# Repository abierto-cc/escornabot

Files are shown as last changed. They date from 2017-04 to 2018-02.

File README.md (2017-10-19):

# furubot

Diseño de robot basado en el Escornabot, completamente hecho en KiCAD. 

Con amor para todo el mundo desde Malmo - Suecia.

# créditos

Los creadores originales de Escornabot www.escornabot.com y su comunidad de usuarios y desarrolladores 

# autor

J. Garcia at abierto.cc

# abierto

Abierto es una inciativa de D. Cuartielles gracias a la generosa aportación de la Fundación PUIG por intermediación de la Fundación Ashoka de cara a contribuir a la creación de material educativo de libre acceso y circulación

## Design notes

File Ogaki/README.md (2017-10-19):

# Escornabot Ogaki

Diseño de robot basado en el Escornabot, completamente hecho en KiCAD. 

Con amor para todo el mundo desde Malmo - Suecia.

# consigue tu kit

Si quieres conseguir el kit para montarlo, visita: https://abierto.cc/shop

# instrucciones de montaje

Puedes ver las instrucciones de montaje paso a paso en: https://sites.google.com/abierto.cc/ogaki

# créditos

Los creadores originales de Escornabot y su comunidad de usuarios y desarrolladores

# autor

J. Garcia at abierto.cc

# abierto

Abierto es una inciativa de D. Cuartielles gracias a la generosa aportación de la Fundación PUIG por intermediación de la Fundación Ashoka de cara a contribuir a la creación de material educativo de libre acceso y circulación

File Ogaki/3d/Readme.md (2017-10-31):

Modelos 3D del Escornabot Ogaki a.k.a. Brivori Compactus v3
===========================================================

Estos son los modelos 3D listos para imprimir para el Escornabot Ogaki. Los ficheros son copias de seguridad de los originales creados por la comunidad Escornabot. Más concretamente:

* El diseño original es por [Xoan Sampaiño][XOA01] ([License MIT][LIC01])
* Las ruedas son de [Rafa
Couto](https://github.com/rafacouto/3d-models/tree/master/escornabot/stronger-wheel) 
* La pieza de sujección de la CPU "EscornaCPU" está basada en el diseño de placa de  [Xabier Rosas](https://github.com/escornabot/electronics).

# Ficheros STL listos para impresión

- Ball-caster [ballcaster.stl](ballcaster.stl)
- Battery bracket [battery-bracket.stl](battery-bracket.stl)
- Motor bracket [motor-bracket.stl](motor-bracket.stl)
- Left wheel [wheel-l.stl](wheel-l.stl)
- Right wheel [wheel-r.stl](wheel-r.stl)
- EscornaCPU 3.00 bracket [escornacpu-3\_00-bracket.stl](escornacpu-3_00-bracket.stl)

Los ficheros fuentes están también en esta carpeta

[LIC01]: brivoi-compactus/LICENSE
[XOA01]: https://github.com/xoan/escornabot

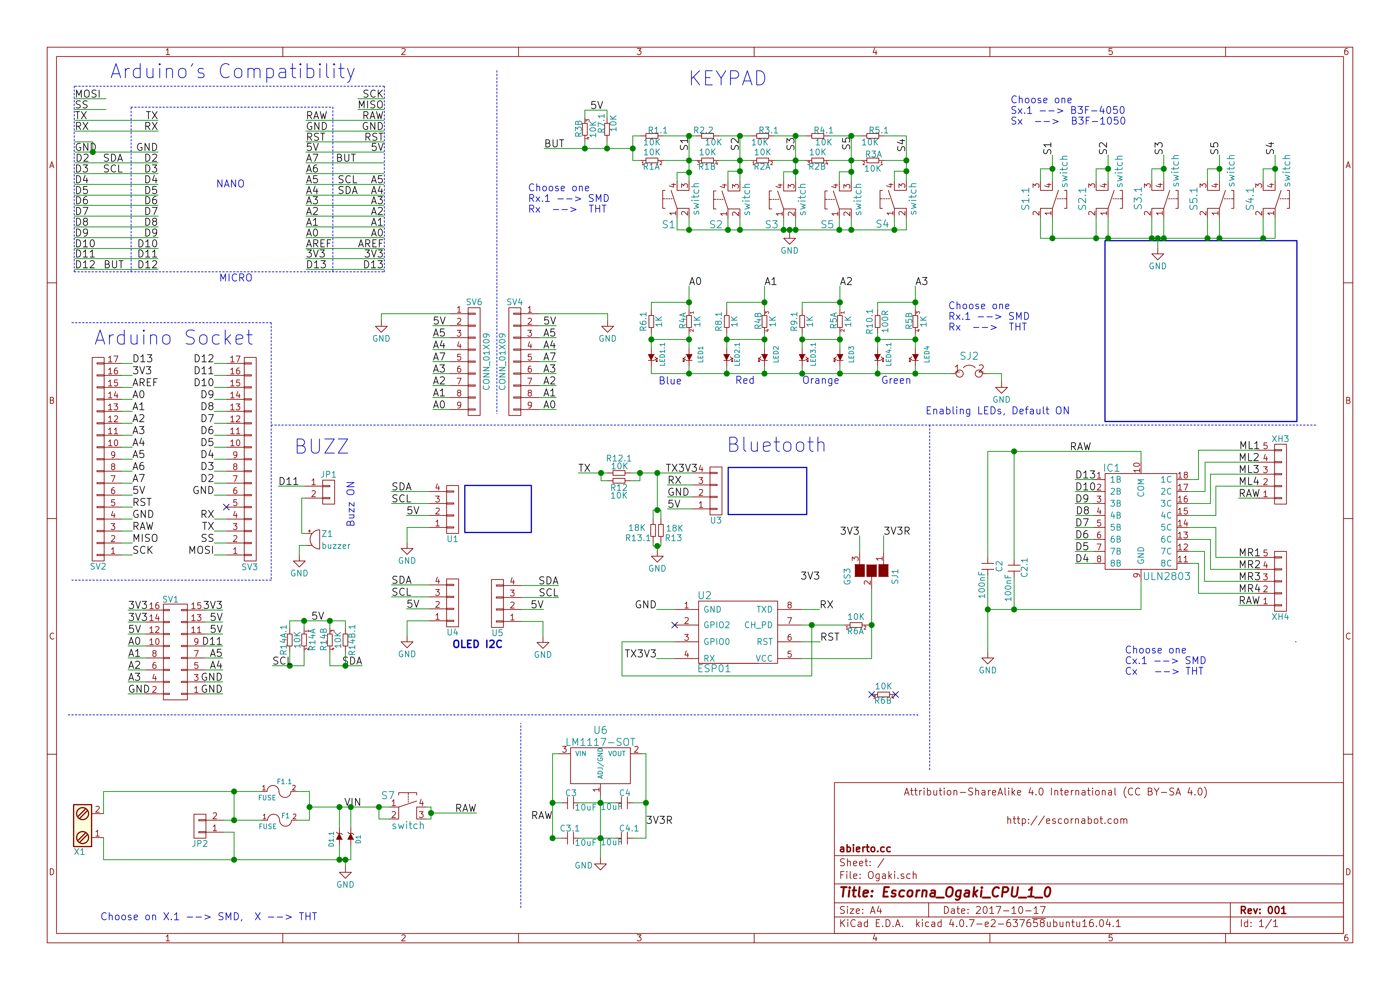
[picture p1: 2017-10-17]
Ogaki/hardware/pdf/Ogaki.png

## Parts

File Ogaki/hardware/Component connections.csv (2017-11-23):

Arduino micro | Arduino Nano | Component
D0 |  |  | D0 | Buetooth (Rx)
D1 |  |  | D1 | Buetooth (Tx)
D2 |  |  |  | Oled (SDA)
D3 |  |  |  | Oled (SCL)
D4 |  |  | D4 | Motor
D5 |  |  | D5 | Motor
D6 |  |  | D6 | Motor
D7 |  |  | D7 | Motor
D8 |  |  | D8 | Motor
D9 |  |  | D9 | Motor
D10 |  |  | D10 | Motor
D11 |  |  | D11 | Buzzer
D12 (A11) |  |  | Buttons
D13 |  |  | D13 | Motor
A0 |  |  | A0 | LED Blue
A1 |  |  | A1 | LED Red
A2 |  |  | A2 | LED Orange
A3 |  |  | A3 | LED Green
 |  |  | A4 | Oled (SDA)
 |  |  | A5 | Oled (SCL)
A6 |  |  | A6
 |  |  | A7 | Buttons

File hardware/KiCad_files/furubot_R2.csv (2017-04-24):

Reference | Value | Footprint | Datasheet
SV1 | CONN_02X08 | Pin_Headers:Pin_Header_Straight_2x08_Pitch2.54mm
R7.1 | 10K | Resistors_SMD:R_0603_HandSoldering
R1.1 | 10K | Resistors_SMD:R_0603_HandSoldering
R3.1 | 10K | Resistors_SMD:R_0603_HandSoldering
R4.1 | 10K | Resistors_SMD:R_0603_HandSoldering
R5.1 | 10K | Resistors_SMD:R_0603_HandSoldering
R2.2 | 10K | Resistors_SMD:R_0603_HandSoldering
S1 | switch | Switch:Button
S2 | switch | Switch:Button
S5 | switch | Switch:Button
S4 | switch | Switch:Button
S5.1 | switch | Buttons_Switches_ThroughHole:SW_PUSH_6mm
S4.1 | switch | Buttons_Switches_ThroughHole:SW_PUSH_6mm
S2.1 | switch | Buttons_Switches_ThroughHole:SW_PUSH_6mm
S3.1 | switch | Buttons_Switches_ThroughHole:SW_PUSH_6mm
S1.1 | switch | Buttons_Switches_ThroughHole:SW_PUSH_6mm
S3 | switch | Switch:Button
R6.1 | 1K | Resistors_SMD:R_0603_HandSoldering
R8.1 | 1K | Resistors_SMD:R_0603_HandSoldering
R9.1 | 1K | Resistors_SMD:R_0603_HandSoldering
R10.1 | 100R | Resistors_SMD:R_0603_HandSoldering
LED1.1 | L | LEDs:LED_0603
LED1 | L | LEDs:LED_D3.0mm
LED2.1 | L | LEDs:LED_0603
LED2 | L | LEDs:LED_D3.0mm
LED3.1 | L | LEDs:LED_0603
LED3 | L | LEDs:LED_D3.0mm
LED4.1 | L | LEDs:LED_0603
LED4 | L | LEDs:LED_D3.0mm
SJ2 | JUMPER | Connect:GS2
JP1 | CONN_01X02 | Pin_Headers:Pin_Header_Straight_1x02_Pitch2.54mm
Z1 | buzzer | Buzzers_Beepers:MagneticBuzzer_StarMicronics_HMB-06_HMB-12
U1 | CONN_01X04 | Pin_Headers:Pin_Header_Straight_1x04_Pitch2.54mm
U4 | CONN_01X04 | Pin_Headers:Pin_Header_Straight_1x04_Pitch2.54mm
U5 | CONN_01X04 | Pin_Headers:Pin_Header_Straight_1x04_Pitch2.54mm
U3 | CONN_01X04 | Pin_Headers:Pin_Header_Straight_1x04_Pitch2.54mm
R12.1 | 10K | Resistors_SMD:R_0603_HandSoldering
R12 | 10K | Resistors_ThroughHole:R_Axial_DIN0204_L3.6mm_D1.6mm_P7.62mm_Horizontal
R13.1 | 18K | Resistors_SMD:R_0603_HandSoldering
R13 | 18K | Resistors_ThroughHole:R_Axial_DIN0204_L3.6mm_D1.6mm_P7.62mm_Horizontal
IC1 | ULN2803 | Housings_DIP:DIP-18_W7.62mm_Socket
C2 | 100nF | Capacitors_ThroughHole:C_Disc_D5.0mm_W2.5mm_P5.00mm
C2.1 | 100nF | Capacitors_SMD:C_0603_HandSoldering
X1 | Screw_Terminal_1x02 | Connect:bornier2
JP2 | CONN_01X02 | Pin_Headers:Pin_Header_Angled_1x02_Pitch2.54mm
F1.1 | FUSE | Resistors_SMD:R_1206_HandSoldering
F1 | FUSE | Fuse_Holders_and_Fuses:Fuse_TE5_Littlefuse-395Series
D1.1 | ZENER | Diodes_SMD:D_0603
D1 | ZENER | Diodes_ThroughHole:D_DO-41_SOD81_P10.16mm_Horizontal
C1 | 100nF | Capacitors_ThroughHole:C_Disc_D5.0mm_W2.5mm_P5.00mm
C1.1 | 100nF | Capacitors_SMD:C_0603_HandSoldering
U2 | ESP01 | escornabot:ESP01
XH4 | CONN_01X05 | user_molex:B5B-XH-A
XH3 | CONN_01X05 | user_molex:B5B-XH-A
R3 | 10K | Resistors_ThroughHole:R_Array_SIP4
R1 | 10K | Resistors_ThroughHole:R_Array_SIP4
R2 | 10K | Resistors_ThroughHole:R_Array_SIP4
R4 | 1K | Resistors_ThroughHole:R_Array_SIP4
R5 | 1K | Resistors_ThroughHole:R_Array_SIP4
R6 | 10K | Resistors_ThroughHole:R_Array_SIP4
S7 | switch | ComponentesVarios:on_off_Switch
SV2 | CONN_01X17 | Pin_Headers:Pin_Header_Straight_1x17_Pitch2.54mm
SV3 | CONN_01X17 | Pin_Headers:Pin_Header_Straight_1x17_Pitch2.54mm
U6 | LM1117-SOT | TO_SOT_Packages_THT:TO-220_Vertical
C4 | 10uF | Capacitors_ThroughHole:C_Disc_D5.0mm_W2.5mm_P5.00mm
C3 | 10uF | Capacitors_ThroughHole:C_Disc_D5.0mm_W2.5mm_P5.00mm
C3.1 | 10uF | Capacitors_SMD:C_0603_HandSoldering
C4.1 | 10uF | Capacitors_SMD:C_0603_HandSoldering
SJ1 | GS3 | Connect:GS3
SV4 | CONN_01X09 | Pin_Headers:Pin_Header_Straight_1x09_Pitch2.54mm
SV6 | CONN_01X09 | Pin_Headers:Pin_Header_Straight_1x09_Pitch2.54mm
R14 | 10K | Resistors_ThroughHole:R_Array_SIP4
R14A.1 | 10K | Resistors_SMD:R_0603_HandSoldering
R14B.1 | 10K | Resistors_SMD:R_0603_HandSoldering

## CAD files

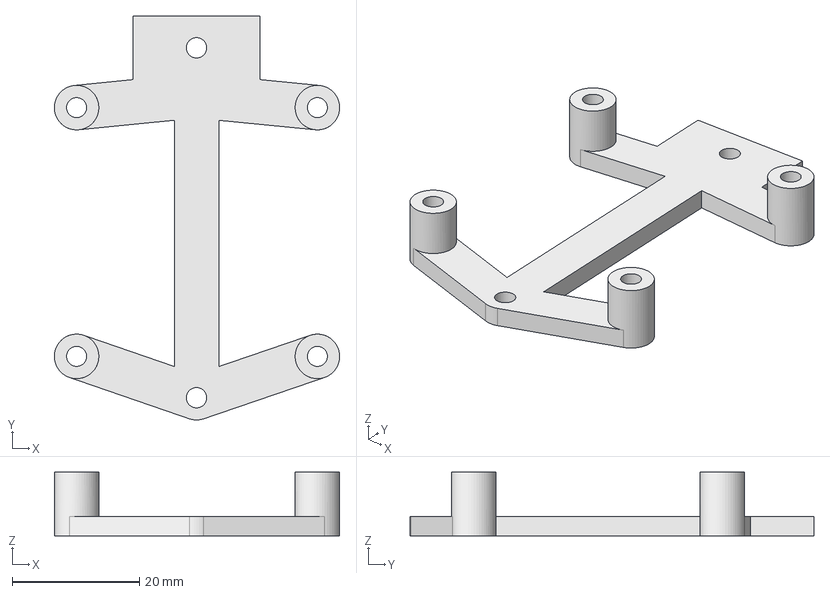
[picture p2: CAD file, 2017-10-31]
Ogaki/3d/escornacpu-3_00-bracket.fcstd
44.8 x 63.5 x 10.0 mm

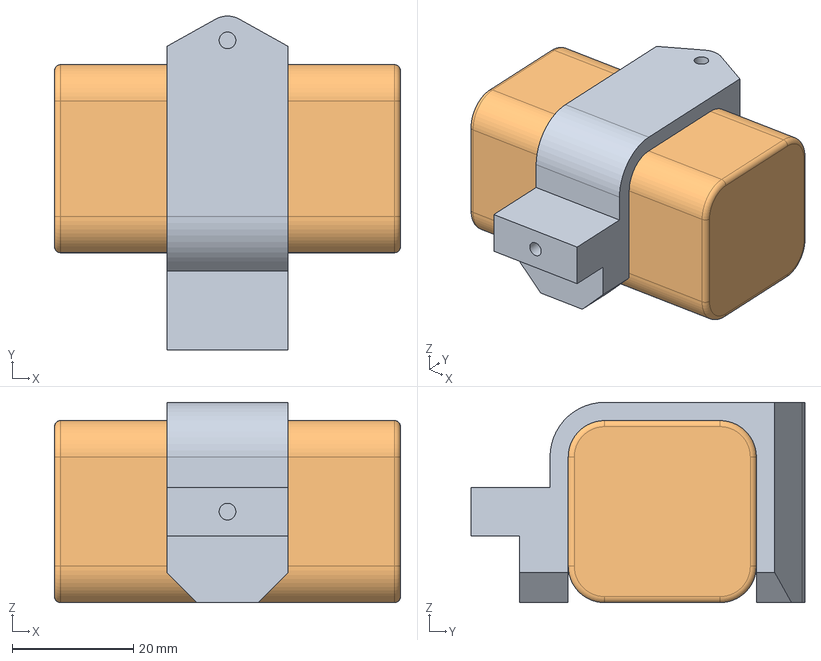
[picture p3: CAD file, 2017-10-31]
Ogaki/3d/battery-bracket.fcstd
57.0 x 55.0 x 33.0 mm
battery-bracket
battery

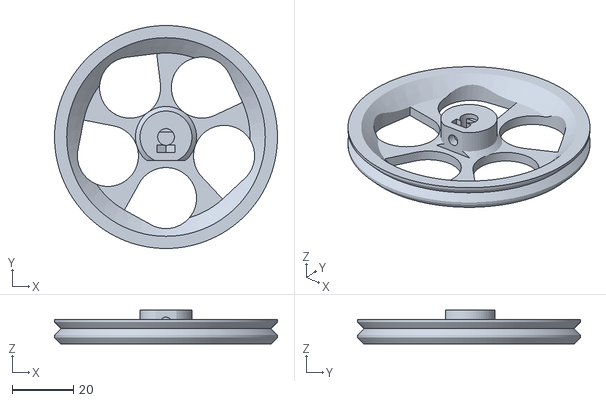
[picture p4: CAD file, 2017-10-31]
Ogaki/3d/wheel-r.stl
73.0 x 73.0 x 11.0

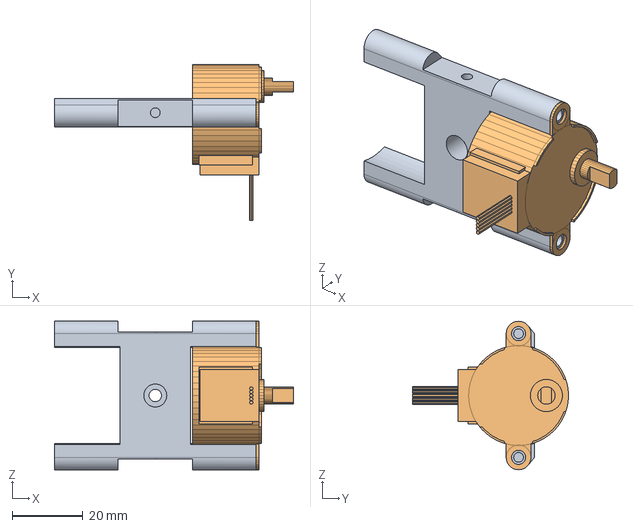
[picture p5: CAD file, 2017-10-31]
Ogaki/3d/motor-bracket.fcstd
67.6 x 44.1 x 42.0 mm
motor-bracket
stepper-motor

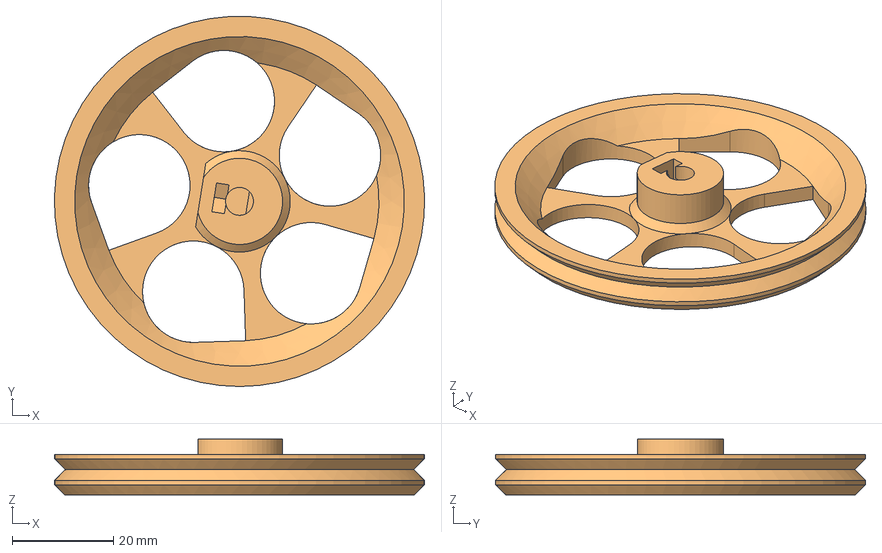
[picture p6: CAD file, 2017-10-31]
Ogaki/3d/wheel.fcstd
73.0 x 72.9 x 11.0 mm
Mirror of PolarPattern
wheel-l

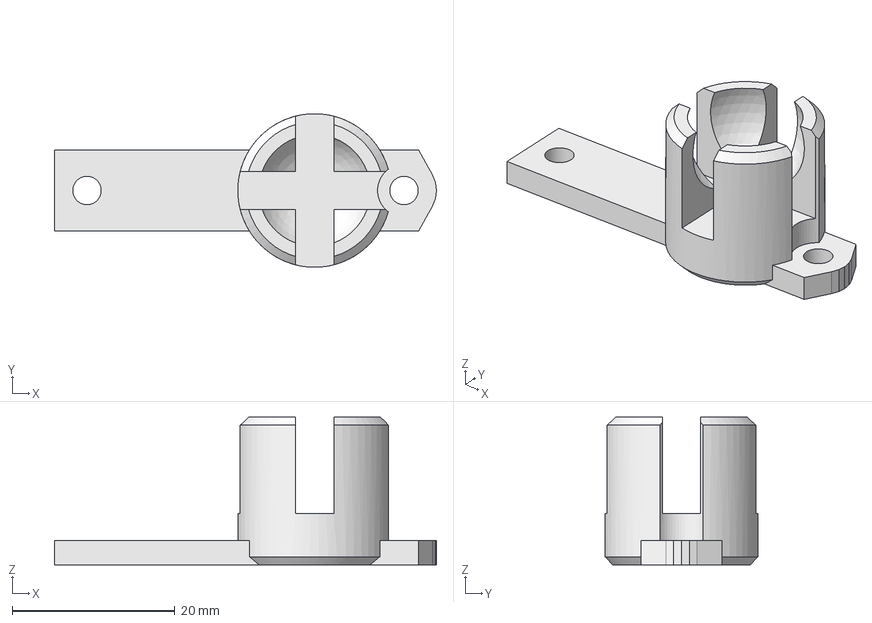
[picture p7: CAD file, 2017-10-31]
Ogaki/3d/ballcaster.fcstd
47.0 x 18.9 x 18.2 mm

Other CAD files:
Ogaki/3d/wheel-l.stl
Ogaki/3d/ballcaster.stl
Ogaki/3d/battery-bracket.stl
Ogaki/3d/escornacpu-3_00-bracket.stl
Ogaki/3d/motor-bracket.stl

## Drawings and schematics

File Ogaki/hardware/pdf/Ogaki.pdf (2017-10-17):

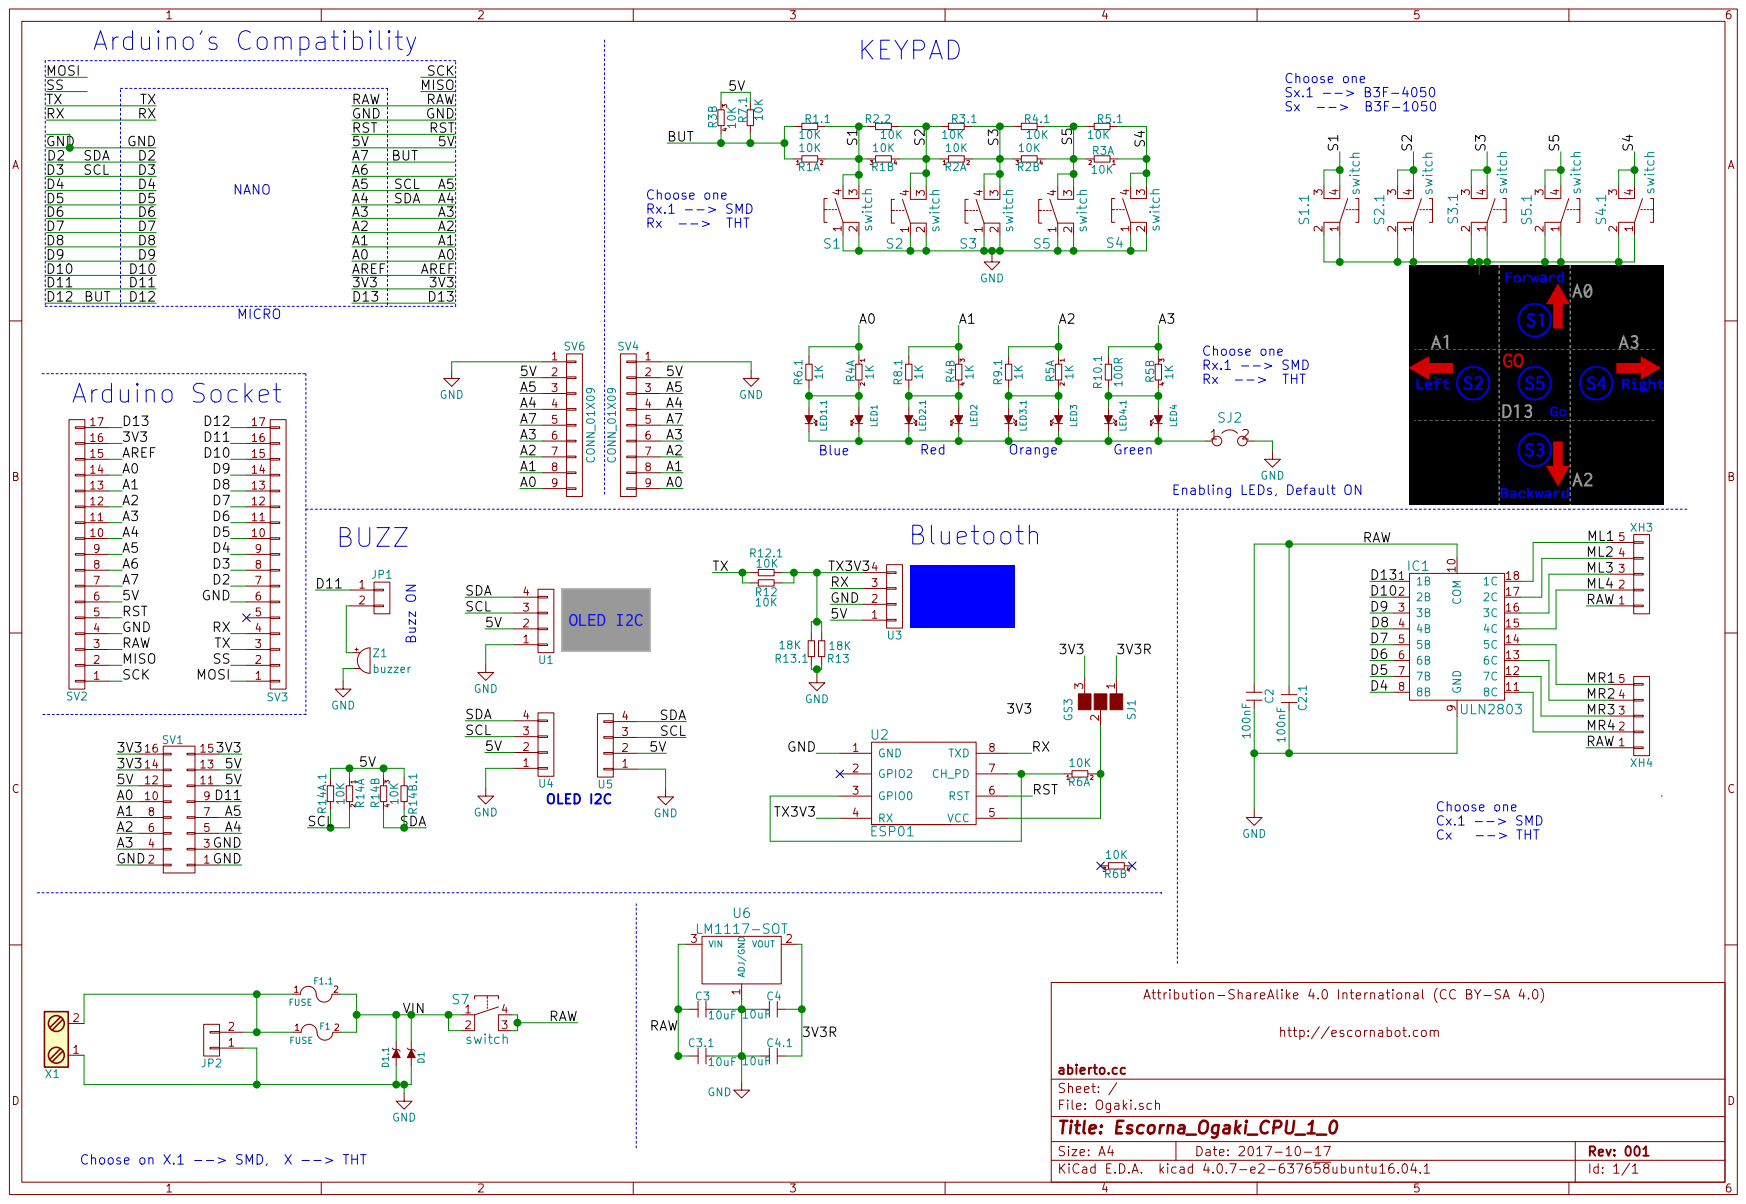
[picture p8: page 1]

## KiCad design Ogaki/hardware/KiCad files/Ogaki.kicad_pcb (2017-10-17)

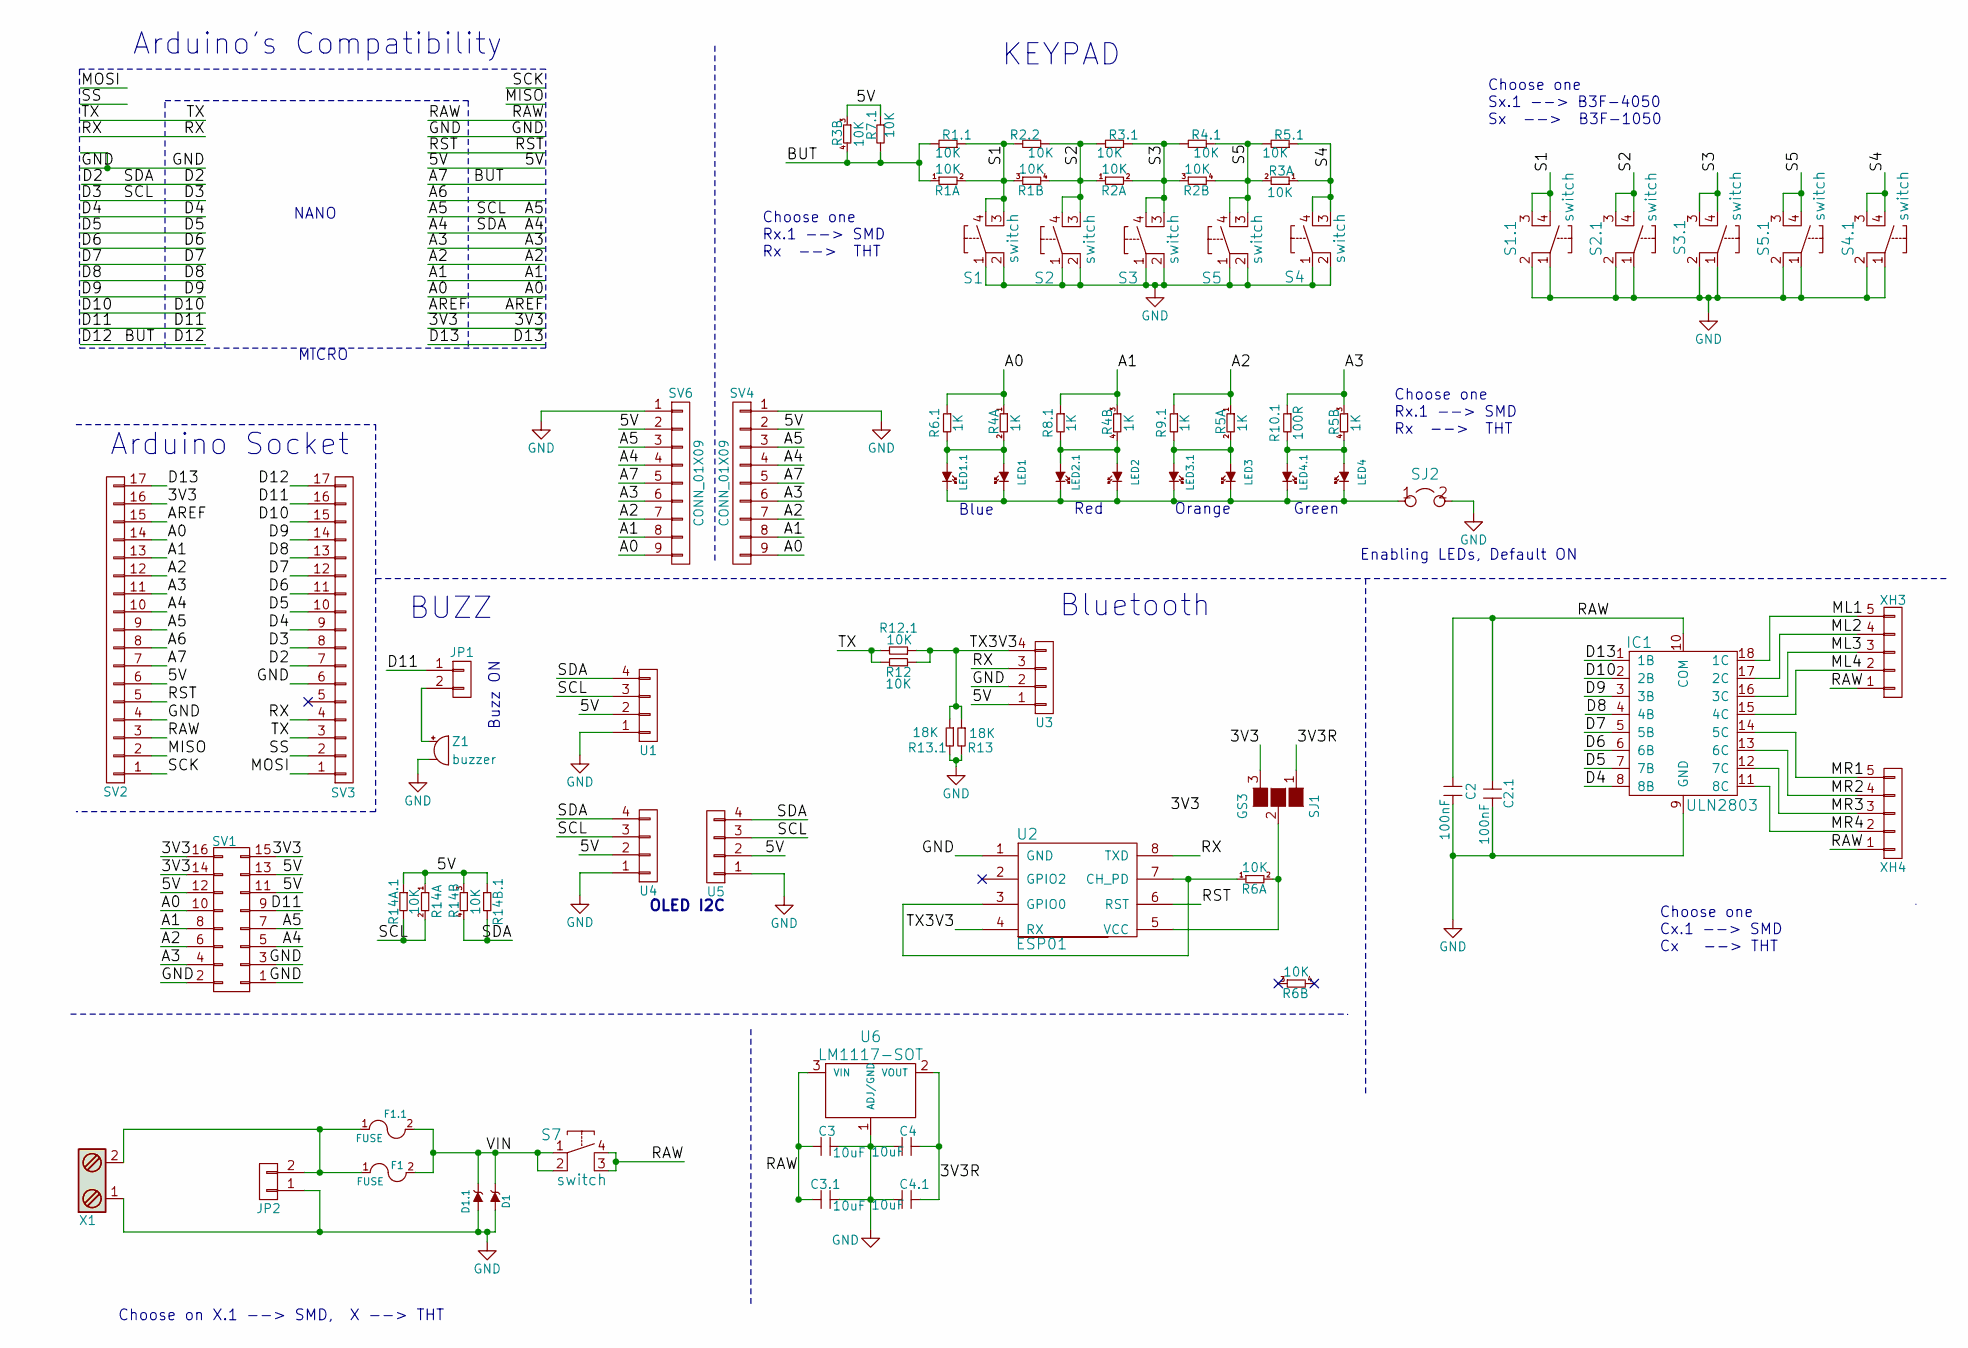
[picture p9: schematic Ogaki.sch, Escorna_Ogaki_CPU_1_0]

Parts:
C2: 100nF; C_Disc_D5.0mm_W2.5mm_P5.00mm
C2.1: 100nF; C_0603_HandSoldering
C3, C4: 10uF; C_Disc_D5.0mm_W2.5mm_P5.00mm
C3.1, C4.1: 10uF; C_0603_HandSoldering
D1: ZENER; D_DO-41_SOD81_P10.16mm_Horizontal
D1.1: ZENER; D_0603
F1: FUSE; Fuse_TE5_Littlefuse-395Series
F1.1: FUSE; R_1206_HandSoldering
IC1: ULN2803; DIP-18_W7.62mm_Socket
JP1: CONN_01X02; Pin_Header_Straight_1x02_Pitch2.54mm
JP2: CONN_01X02; Pin_Header_Angled_1x02_Pitch2.54mm
LED1, LED2, LED3, LED4: L; LED_D3.0mm
LED1.1, LED2.1, LED3.1, LED4.1: L; LED_0603
R1, R2, R3, R6, R14: 10K; R_Array_SIP4
R1.1, R2.2, R3.1, R4.1, R5.1, R7.1, R12.1, R14A.1, R14B.1: 10K; R_0603_HandSoldering
R4, R5: 1K; R_Array_SIP4
R6.1, R8.1, R9.1: 1K; R_0603_HandSoldering
R10.1: 100R; R_0603_HandSoldering
R12: 10K; R_Axial_DIN0204_L3.6mm_D1.6mm_P7.62mm_Horizontal
R13: 18K; R_Axial_DIN0204_L3.6mm_D1.6mm_P7.62mm_Horizontal
R13.1: 18K; R_0603_HandSoldering
S1, S2, S3, S4, S5: switch; Button
S1.1, S2.1, S3.1, S4.1, S5.1: switch; SW_PUSH_6mm
S7: switch; on_off_Switch
SJ1: GS3
SJ2: JUMPER; GS2
SV1: CONN_02X08; Pin_Header_Straight_2x08_Pitch2.54mm
SV2, SV3: CONN_01X17; Pin_Header_Straight_1x17_Pitch2.54mm
SV4, SV6: CONN_01X09; Pin_Header_Straight_1x09_Pitch2.54mm
U1, U3, U4, U5: CONN_01X04; Pin_Header_Straight_1x04_Pitch2.54mm
U2: ESP01
U6: LM1117-SOT; TO-220_Vertical
X1: Screw_Terminal_1x02; bornier2
XH3, XH4: CONN_01X05; B5B-XH-A
Z1: buzzer; MagneticBuzzer_StarMicronics_HMB-06_HMB-12

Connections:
/3V3: SJ1.3 (G3), SV1.14, SV1.15, SV1.16, SV2.16
/3V3R: C4.1, C4.1.1, SJ1.1 (G1), U6.2 (VOUT)
/5V: R3.3, R7.1.1, R14.1, R14.3, R14A.1.1, R14B.1.1, SV1.11, SV1.12, SV1.13, SV2.6, SV4.2, SV6.2, U1.2, U3.1, U4.2, U5.2
/A0: R4.1, R6.1.1, SV1.10, SV2.14, SV4.9, SV6.9
/A1: R4.3, R8.1.1, SV1.8, SV2.13, SV4.8, SV6.8
/A2: R5.1, R9.1.1, SV1.6, SV2.12, SV4.7, SV6.7
/A3: R5.3, R10.1.1, SV1.4, SV2.11, SV4.6, SV6.6
/A4: R14.4, R14B.1.2, SV1.5, SV2.10, SV3.7, SV4.4, SV6.4, U1.4, U4.4, U5.4
/A5: R14.2, R14A.1.2, SV1.7, SV2.9, SV3.8, SV4.3, SV6.3, U1.3, U4.3, U5.3
/A6: SV2.8
/A7: R1.1, R1.1.2, R3.4, R7.1.2, SV2.7, SV3.17, SV4.5, SV6.5
/AREF: SV2.15
/D4: IC1.8 (8B), SV3.9
/D5: IC1.7 (7B), SV3.10
/D6: IC1.6 (6B), SV3.11
/D7: IC1.5 (5B), SV3.12
/D8: IC1.4 (4B), SV3.13
/D9: IC1.3 (3B), SV3.14
/D10: IC1.2 (2B), SV3.15
/D11: JP1.1, SV1.9, SV3.16
/D13: IC1.1 (1B), SV2.17
/MISO: SV2.2
/ML1: IC1.18 (1C), XH3.5
/ML2: IC1.17 (2C), XH3.4
/ML3: IC1.16 (3C), XH3.3
/ML4: IC1.15 (4C), XH3.2
/MOSI: SV3.1
/MR1: IC1.14 (5C), XH4.5
/MR2: IC1.13 (6C), XH4.4
/MR3: IC1.12 (7C), XH4.3
/MR4: IC1.11 (8C), XH4.2
/RAW: C2.2, C2.1.2, C3.2, C3.1.2, IC1.10 (COM), S7.3, S7.4, SV2.3, U6.3 (VIN), XH3.1, XH4.1
/RST: SV2.5, U2.6 (RST)
/RX: SV3.4, U2.8 (TXD), U3.3
/S1: R1.2, R1.3, R1.1.1, R2.2.2, S1.3, S1.4, S1.1.3, S1.1.4
/S2: R1.4, R2.1, R2.2.1, R3.1.2, S2.3, S2.4, S2.1.3, S2.1.4
/S3: R2.2, R2.3, R3.1.1, R4.1.2, S3.3, S3.4, S3.1.3, S3.1.4
/S4: R3.1, R5.1.1, S4.3, S4.4, S4.1.3, S4.1.4
/S5: R2.4, R3.2, R4.1.1, R5.1.2, S5.3, S5.4, S5.1.3, S5.1.4
/SCK: SV2.1
/SS: SV3.2
/TX: R12.2, R12.1.2, SV3.3
/TX3V3: R12.1, R12.1.1, R13.1, R13.1.1, U2.4 (RX), U3.4
/VIN: D1.1 (K), D1.1.1 (K), F1.2, F1.1.2, S7.1, S7.2
GND: C2.1, C2.1.1, C3.1, C3.1.1, C4.2, C4.1.2, D1.2 (A), D1.1.2 (A), IC1.9 (GND), JP2.1, R13.2, R13.1.2, S1.1, S1.2, S1.1.1, S1.1.2, S2.1, S2.2, S2.1.1, S2.1.2, S3.1, S3.2, S3.1.1, S3.1.2, S4.1, S4.2, S4.1.1, S4.1.2, S5.1, S5.2, S5.1.1, S5.1.2, SJ2.2, SV1.1, SV1.2, SV1.3, SV2.4, SV3.6, SV4.1, SV6.1, U1.1, U2.1 (GND), U3.2, U4.1, U5.1, U6.1 (ADJ/GND), X1.1, Z1.2; also elsewhere on the board
unnamed: F1.1, F1.1.1, JP2.2, X1.2
unnamed: JP1.2, Z1.1
unnamed: LED1.1 (K), LED1.1.1 (K), LED2.1 (K), LED2.1.1 (K), LED3.1 (K), LED3.1.1 (K), LED4.1 (K), LED4.1.1 (K), SJ2.1
unnamed: LED1.2 (A), LED1.1.2 (A), R4.2, R6.1.2
unnamed: LED2.2 (A), LED2.1.2 (A), R4.4, R8.1.2
unnamed: LED3.2 (A), LED3.1.2 (A), R5.2, R9.1.2
unnamed: LED4.2 (A), LED4.1.2 (A), R5.4, R10.1.2
unnamed: R6.1, U2.3 (GPIO0), U2.7 (CH_PD)
unnamed: R6.2, SJ1.2 (G2), U2.5 (VCC)

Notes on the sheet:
MICRO
NANO
Arduino's Compatibility
Arduino Socket
Choose one Rx.1 --> SMD Rx --> THT
Choose one Sx.1 --> B3F-4050 Sx --> B3F-1050
KEYPAD
Enabling LEDs, Default ON
BUZZ
Buzz ON
OLED I2C
Bluetooth
Choose one Cx.1 --> SMD Cx --> THT
Choose on X.1 --> SMD, X --> THT
Blue
Red
Orange
Green

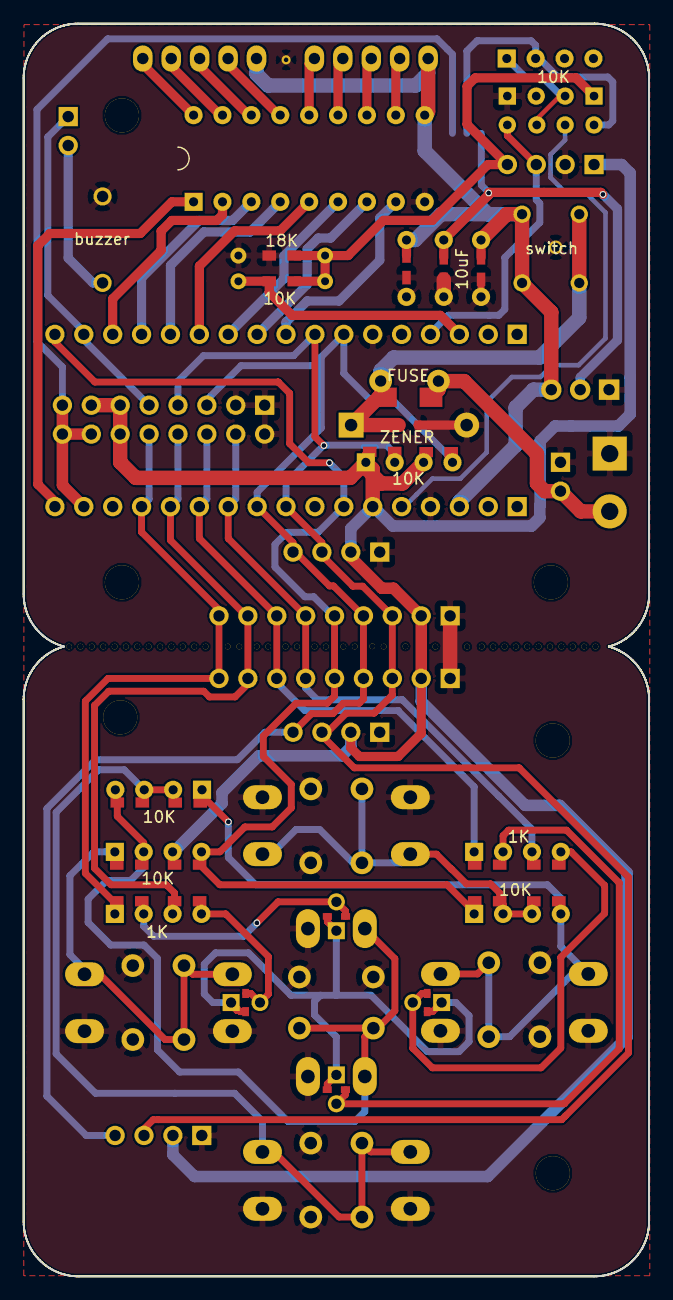
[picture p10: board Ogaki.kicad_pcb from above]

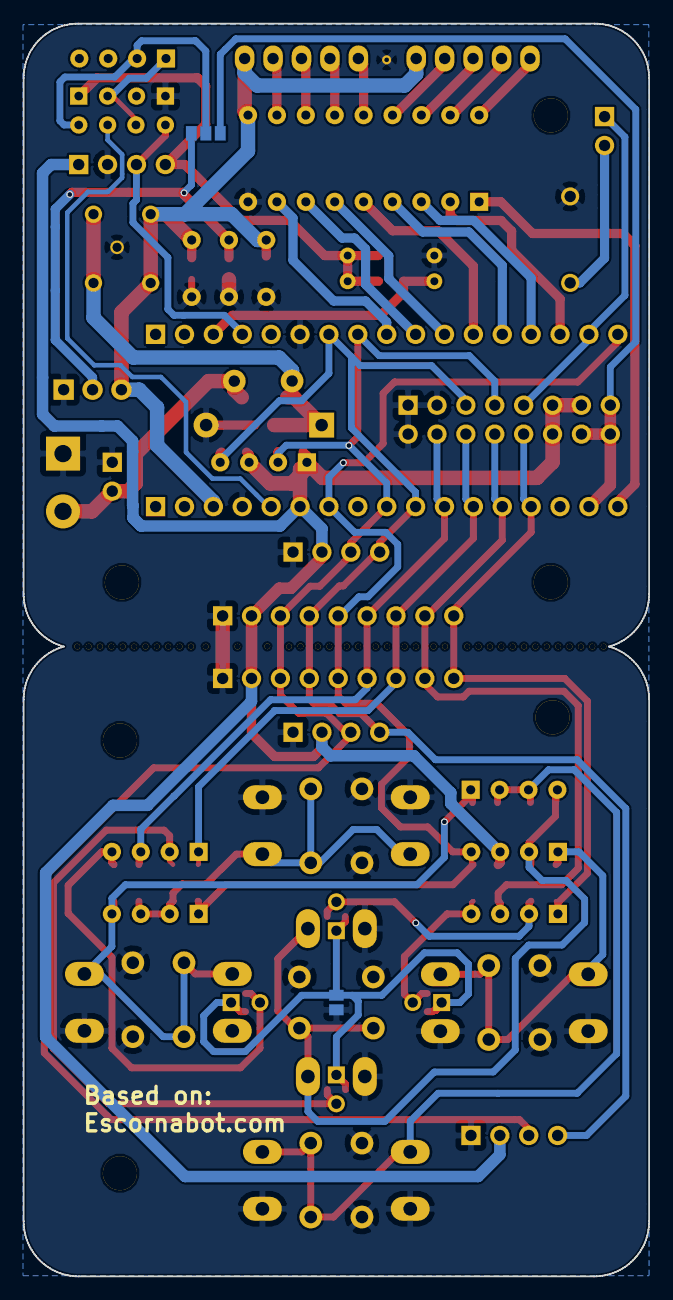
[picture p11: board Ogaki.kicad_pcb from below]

Board: 2 copper layers, 55.0 x 110.1 mm, 75 parts (3 on the bottom side), 48 nets.

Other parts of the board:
GND: GND; SolderWirePad_single_0-8mmDrill
svg2mod, svg2mod#2: G***; svg2mod

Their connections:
GND: GND.1; also elsewhere on the board

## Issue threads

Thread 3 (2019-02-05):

Ogaki adafruit motor pin configuration change and step change.

raspe827, 2019-02-05:
The Ogaki shipped with motors from adafruit does not behave as previous model since the gear ratio of the motors and the pin configuration in the motor contact is changed as well.

There are however a quick fix done on this so that the Escornabot behaves as normal or at least close to normal.

A suggestion is that the code should be re written so it would be easy to change the motor configuration from Escornabot.ino

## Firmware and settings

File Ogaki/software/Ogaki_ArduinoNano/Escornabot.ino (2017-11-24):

// Escornabot.ino
/*

Copyright (C) 2014 Bricolabs - http://bricolabs.cc

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
See LICENSE.txt for details

*/

#include "Bot.h"

//////////////////////////////////////////////////////////////////////

// instance
Bot ESCORNABOT;

//////////////////////////////////////////////////////////////////////

void setup()
{
    ESCORNABOT.init();
}

//////////////////////////////////////////////////////////////////////

void loop()
{
  Serial.println(analogRead(A7));
  
    ESCORNABOT.loop();
}

//////////////////////////////////////////////////////////////////////


// EOF

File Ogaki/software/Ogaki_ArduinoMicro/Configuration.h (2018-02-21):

// Configuration.h
/*

Copyright (C) 2014 Bricolabs - http://bricolabs.cc

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
See LICENSE.txt for details

*/

#ifndef _CONFIGURATION_H
#define _CONFIGURATION_H


//////////////////////////////////////////////////////////////////////
///// general configuration
//////////////////////////////////////////////////////////////////////

// engine to use
#define ENGINE_TYPE_STEPPERS

// button set to use
#define BUTTONS_ANALOG
//#define BUTTONS_DIGITAL
//#define BUTTONS_BLUETOOTH

// milliseconds after a button is considered as pressed
#define BUTTON_MIN_PRESSED 30

// milliseconds after a button is considered as long pressed
#define BUTTON_LONG_PRESSED 1000

// put to false to add movements to the program after its execution
#define PROGRAM_RESET_ALWAYS true

// store configuration and program within internal EEPROM
#define USE_PERSISTENT_MEMORY true

// memory capacity for program movements
#define MOVE_LIMIT 100

// milliseconds for the "pause" movement
#define PAUSE_MOVE_MILLIS 1000

// milliseconds delay before starting to move
#define DELAY_BEFORE_GO 500

// milliseconds to pause after every movement
#define AFTER_MOVEMENT_PAUSE 0

// point of view set when Vacalourabot is started
#define POV_INITIAL	POV_ESCORNABOT

// buzzer
#define USE_BUZZER true
#define BUZZER_PIN 11
#define PROGRAM_FINISHED_RTTL RTTL_FIDO

// simple led
#define USE_SIMPLE_LED true
#define SIMPLE_LED_PIN A0



//////////////////////////////////////////////////////////////////////
///// Steppers engine setup
//////////////////////////////////////////////////////////////////////

#ifdef ENGINE_TYPE_STEPPERS

// stepper pin setup (digital outputs)
#define STEPPERS_MOTOR_RIGHT_IN1 7
#define STEPPERS_MOTOR_RIGHT_IN2 6
#define STEPPERS_MOTOR_RIGHT_IN3 5
#define STEPPERS_MOTOR_RIGHT_IN4 4
#define STEPPERS_MOTOR_LEFT_IN1 13
#define STEPPERS_MOTOR_LEFT_IN2 10
#define STEPPERS_MOTOR_LEFT_IN3 9
#define STEPPERS_MOTOR_LEFT_IN4 8

// step calibration
#define STEPPERS_STEPS_PER_SECOND 1000
#define STEPPERS_LINE_STEPS 1738
#define STEPPERS_TURN_STEPS 1024

#endif



//////////////////////////////////////////////////////////////////////
///// Button set digital
//////////////////////////////////////////////////////////////////////

#ifdef BUTTONS_DIGITAL

// Button set pin setup (digital or analog inputs)
#define BS_DIGITAL_UP A0
#define BS_DIGITAL_RIGHT A1
#define BS_DIGITAL_DOWN A2
#define BS_DIGITAL_LEFT A3
#define BS_DIGITAL_GO A4
#define BS_DIGITAL_RESET A5

#endif // BUTTONS_DIGITAL



//////////////////////////////////////////////////////////////////////
///// Button set analog
//////////////////////////////////////////////////////////////////////

#ifdef BUTTONS_ANALOG

#define BS_ANALOG_WIRES 2
//#define BS_ANALOG_WIRES 3

// Button set pin setup (analog input)
#define BS_ANALOG_PIN A11

// input values for each key pressed (0 if key doesn't exist)
#define BS_ANALOG_VALUE_UP 813
#define BS_ANALOG_VALUE_RIGHT 738
#define BS_ANALOG_VALUE_DOWN 578
#define BS_ANALOG_VALUE_LEFT 886
#define BS_ANALOG_VALUE_GO 857
#define BS_ANALOG_VALUE_RESET 448

#endif // BUTTONS_ANALOG



//////////////////////////////////////////////////////////////////////
///// Button set Bluetooth
//////////////////////////////////////////////////////////////////////

#ifdef BUTTONS_BLUETOOTH

// Arduino serial port
#define BS_BLUETOOTH_SERIAL	Serial
//#define BS_BLUETOOTH_SERIAL	Serial1
//#define BS_BLUETOOTH_SERIAL	Serial2
//#define BS_BLUETOOTH_SERIAL	Serial3

#define BS_BLUETOOTH_BAUDS 9600

#endif // BUTTONS_BLUETOOTH




//////////////////////////////////////////////////////////////////////
//////////////////////////////////////////////////////////////////////


#endif // _CONFIGURATION_H

// EOF

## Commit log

2017-04-07 Añadidos ficheros de diseño
    [escornabot_v3.csv, escornabot_v3.kicad_pcb, escornabot_v3.sch]
2017-04-07 revised folder structure
    [escornabot_v3.csv, escornabot_v3.kicad_pcb, escornabot_v3.sch]
2017-04-07 deleted old files
    [escornabot_v3.csv, escornabot_v3.kicad_pcb, escornabot_v3.sch]
2017-04-07 fixed folder name
    [escornabot_v3.csv, escornabot_v3.kicad_pcb, escornabot_v3.sch]
2017-04-07 Actualización del fichero de layout con las cotas de los drills para la fijacion
    [escornabot_v3.kicad_pcb]
2017-04-24 Actualizacion hardware
    Corrección de errores
    [escornabot_v3.kicad_pcb]
2017-04-25 Actualización de hardware
    [furubot_R2-B.Cu.gbl, furubot_R2-B.Mask.gbs, furubot_R2-B.SilkS.gbo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]
2017-05-05 Actualizacion hardware
    [furubot_R2-B.Cu.gbl, furubot_R2-B.Mask.gbs, furubot_R2-B.SilkS.gbo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]
2017-05-24 Actualización a Egaki
    [Egaki.csv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]
2017-09-15 Firmware Furubot
    Adaptación del código de Escornabot para la versión Ogaki
    [Configuration.h]
2017-10-17 Actualización a la version Ogaki
    [Egaki.csv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]
2017-10-17 Esquemáticos
    Archivos png y pdf de los esquemáticos del Joselito mini
2017-10-17 Silks
    Archivos de borde de placa en formato de componente para KiCad
2017-10-17 Actualización a la verison Ogaki
    [Configuration.h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]
2017-10-17 Esquemáticos
    Archivos png y pdf de los esquemáticos del Escornabot Ogaki
2017-10-17 Dimensiones
    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
2017-10-17 KiCad files
    Archivos de diseño en KiCad del Escornabot Ogaki
    [Ogaki.csv, Ogaki.kicad_pcb, Ogaki.sch]
2017-10-17 Gerbers
    Archivos para fabricación de PCB delEscornabot Ogaki
    [Ogaki-B.Cu.gbl, Ogaki-B.Mask.gbs, Ogaki-B.SilkS.gbo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]
2017-10-17 Firmware
    Adaptación del código original de Escornabot a la versión Ogaki
    [Configuration.h]
2017-10-19 BOM Ogaki
    Lista de los componentes necesarios para el montaje completo de la electrónica de la versión Ogaki de Escornabot
2017-10-19 BOM Ogaki
    Lista de componentes para la versión Ogaki de Escornabot
2017-10-19 BOM Ogaki
    [BOM Ogaki.csv]
2017-10-19 Actualizado el Readme... Amigos!!
2017-10-19 Actualizado el Readme
2017-10-21 added 3D models
    [ballcaster.stl, battery-bracket.stl, escornacpu-3_00-bracket.stl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]
2017-10-21 added source files for 3d models
    [ballcaster.fcstd, battery-bracket.fcstd, escornacpu-3_00-bracket.fcstd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]
2017-10-31 Esquemas
    Archivos png y pdf de los esquemas del Escornabot Ogaki
2017-11-23 Conexiones
    Archivo con las conexiones de los componentes de Ogaki para Arduino Micro y Arduino Nano
    [Component connections.csv]
2017-11-24 Actualización de software
    Añadido el software para Ogaki con Arduino Nano
    [Configuration.h]
2018-02-07 Instrucciones de montaje del chasis
    Hemos añadido un documento con las instruccionesde montaje del chasis de Ogaki
2018-02-07 Instrucciones de montaje del chasis
    Documento con las instruccionesde montaje del chasis de Ogaki
2018-02-14 Update Configuration.h
    SIMPLE_LED_PIN y BUZZER_PIN, utilizan el mismo PIN, por lo que el buzzer no para de pitar :)
    [Configuration.h]

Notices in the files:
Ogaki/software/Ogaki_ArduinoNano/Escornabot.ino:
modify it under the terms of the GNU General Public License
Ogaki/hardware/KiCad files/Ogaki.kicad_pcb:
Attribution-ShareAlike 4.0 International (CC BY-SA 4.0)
